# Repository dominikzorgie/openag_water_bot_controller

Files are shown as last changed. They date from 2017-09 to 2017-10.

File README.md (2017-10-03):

# OpenAg Waterbot Controller
Printed Circuit Board (PCB) that enables computer control for nutrient dosing in the Food Server (FS)

## Contents
- [Specification](documentation/spec.md) - High level description of the system.
- Bill of Materials
  - [PCB BOM](documentation/pcb_bom.csv) - all components required to assemble the PCB only. Includes microcontrollers, diodes, relays, resistors, etc.
  - [Enclosure BOM](documentation/enclosure_bom.csv) - All components required to assemble the encolsure around the PCB. Includes encapsulation shell, connectors, wire, potting, etc.
  - [Wiring Harness BOM](documentation/wiring_harness_bom.csv) - All components required to assemble the wiring harnesses for connecting the waterbot controller to the solenoids and brain box. Includes connectors, wires, heat shrink, etc.
  - [Tool BOM](documentation/tool_bom.csv) - All tools required to fabricate the enclosure and wire harnesses. Includes potting dispenser gun, powerpole crimper, etc.

## System Block Diagram
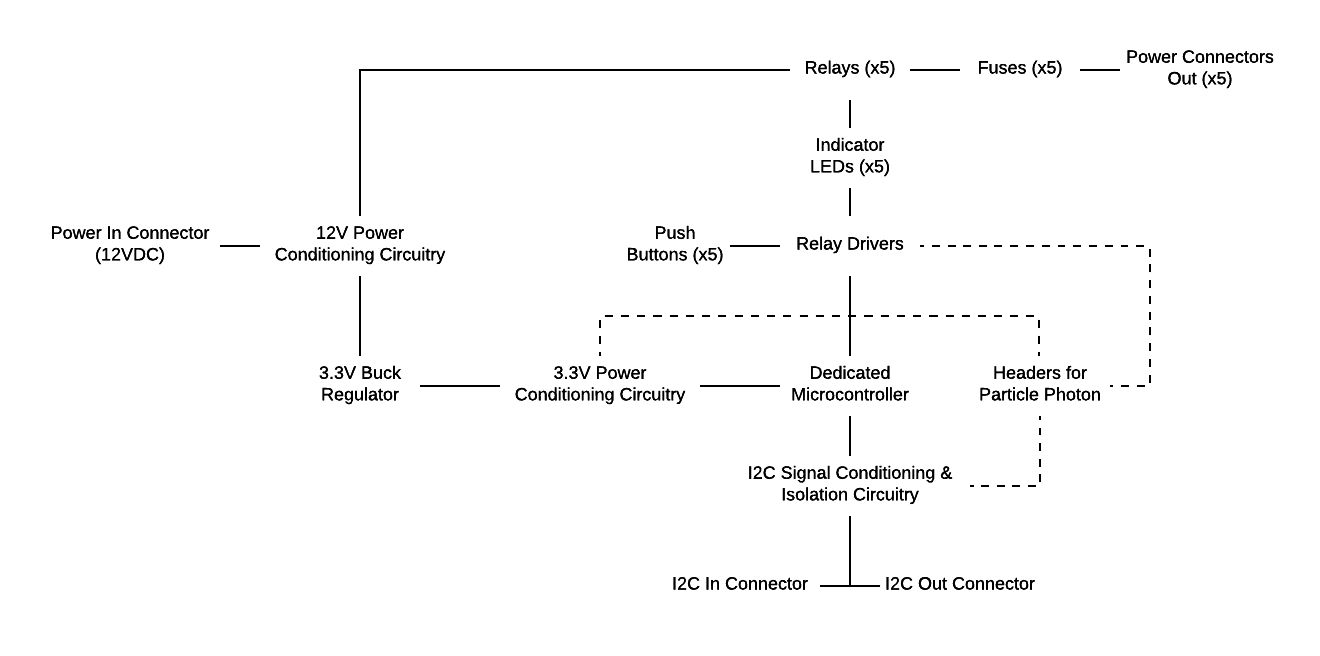
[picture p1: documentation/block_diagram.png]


## Connection Diagram
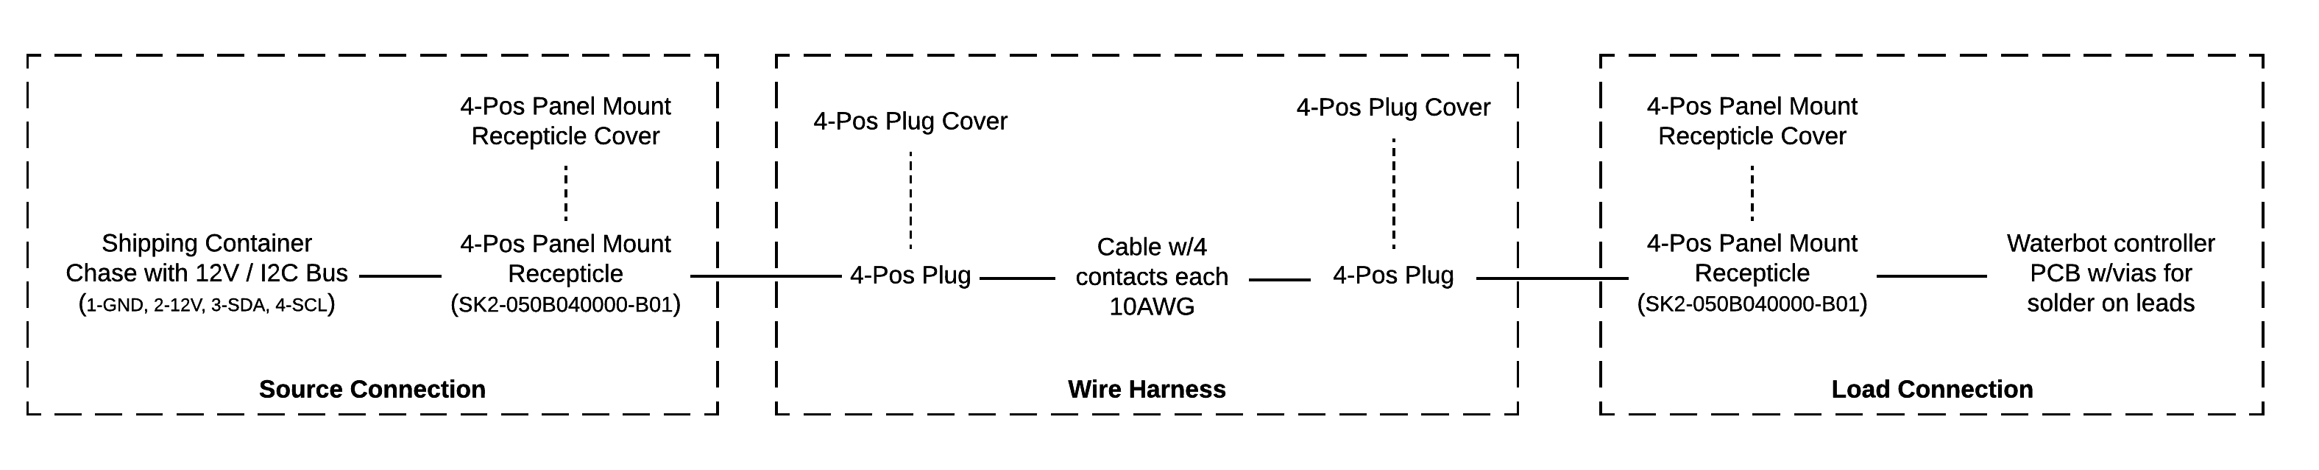
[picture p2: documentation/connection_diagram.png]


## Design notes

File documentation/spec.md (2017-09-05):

# OpenAg Water Bot Controller Specification

## Objective
The Open Agriculture Initiative at MIT's Media Lab is developing a Food Server, a shipping container sized unit outfitted with sensors and actuators for creating an automated control environment for hydroponic plant growth research.

A major component to the Food Server design is the Water Bot, a device for precisely controlling nutrient delivery to the plants. The Water Bot has five solenoid valves that must be controlled from a computer. The Water Bot Controller PCB will provide such control.

## Features
- Device will communicate via I2C with the Brain Box, the master control device built around the Beaglebone Black.
- Device will be powered from the 12VDC power lines running throughout the Food Server. 
- Device will be able to control the power to x5 12V-2A solenoids
- Device will have the option for manual control via pushbuttons that turn on/off the solenoids.
- Device will have a dedicated, low-cost onboard microcontroller that can be programmed to communicate via I2C and send high/low signals to the relay drivers to turn on/off the solenoids. 
- Device will have optional headers and zero-ohm resistor pads for connecting a Particle Photon in order to make the PCB a standalone IoT device. 
- Best practices will be followed to minimize electromagnetic interference throughout the device. 
- As the device will operate inside an environment that is subjected to high humidities and water splashing, all signal and power connectors will have an IP67 rating and the assembled PCB (PCBA) will be conformally coated.
- Device will integrate with mechanical mount on the side of each grow rack. The PCB will be no larger than 8"x8"

## Block Diagram
Block Diagram

## Supporting Documents
- Brain PCB V1 schematic & board files 
- Brain PCB V1 datasheets
- Example PSoC 4000 schematic & board files

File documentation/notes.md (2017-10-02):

on psoc4000 micro, for power config, using unregulated external supply
see fig 9 in datasheet
why are we using 1uF instead of 0.1uF?

what logic level i2c should we use?
psoc4000 provides a separate voltage domain for P3.0, P3.1, P3.2 via VDDIO
P3.0 and P3.1 are also SDAT and SCLK respectively
enables communicating w/system running at different voltage (VDDIO < VDD)
e.g. VDD can be 3.3V and VDDIO can be 1.8V
---never mind, the 16 pin SOIC does not have a VDDIO pin

what is the current draw on micro?..trying to spec voltage regulator
input voltage is 12V, output voltage is 3.3V
I_dd_11 max 4.5mA (when in active mode executing from flash w/cpu at 16mhz...see table 4)
Idiode max 100uA (table 6)
Itot_gpio max 85 mA (table 6)
spec regulator for >100mA

current draw on relay coil?
- @12VDC, 33.3mA

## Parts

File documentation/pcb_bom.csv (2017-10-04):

Qty | Description | Unit Cost | Sum Cost | MFG | MFG P/N | Vendor | Vendor P/N | Link
MICROCONTROLLERS
1 | IC MCU 32BIT 8KB FLASH 16SOIC | 1.18 | 1.18 | Cypress Semiconductor Corp | CY8C4013SXI-411 | Digikey | CY8C4013SXI-411-ND | https://www.digikey.com/product-detail/en/cypress-semiconductor-corp/CY8C4013SXI-411/CY8C4013SXI-411-ND/4842997
REGULATORS
1 | IC REG LINEAR 5V 100MA SOT23-3 | 0.92 | 0.92 | Texas Instruments | LM3480IM3-5.0/NOPB | Digikey | LM3480IM3-5.0/NOPBCT-ND | https://www.digikey.com/product-detail/en/texas-instruments/LM3480IM3-5.0-NOPB/LM3480IM3-5.0-NOPBCT-ND/270751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
DIODES
? | DIODE GEN PURP 75V 200MA SOT23-3 | 0.2 | ? | Diodes Incorporated | MMBD4148-7-F | Digikey | MMBD4148-FDICT-ND | https://www.digikey.com/product-detail/en/diodes-incorporated/MMBD4148-7-F/MMBD4148-FDICT-ND/815711
1 | TVS DIODE 14VWM 23.2VC SMA | 0.42 | 0.42 | Littlefuse | SMAJ14A | Digikey | SMAJ14ALFCT-ND | https://www.digikey.com/product-detail/en/littelfuse-inc/SMAJ14A/SMAJ14ALFCT-ND/762486
? | LED BLUE CLEAR 0603 SMD | 0.49 | ? | Kingbright | APT1608QBC/D | Digikey | 754-1434-1-ND | https://www.digikey.com/product-detail/en/kingbright/APT1608QBC-D/754-1434-1-ND/2163792
CAPACITORS
1 | CAP CER 0.1UF 50V X7R 1206 | 0.69 | 0.69 | Johansen Dielectrics | 500X18W104MV4E | Digikey | 709-1013-1-ND | https://www.digikey.com/product-detail/en/johanson-dielectrics-inc/500X18W104MV4E/709-1013-1-ND/1556418
RELAYS
? | RELAY GEN PURPOSE SPDT 10A 12V | 1.33 | ? | Omron Electronics | G5LE-14 DC12 | Digikey | Z1012-ND | https://www.digikey.com/product-detail/en/omron-electronics-inc-emc-div/G5LE-14-DC12/Z1012-ND/280369
SWITCHES
? | SWITCH TACTILE SPST-NO 0.05A 24V | 0.37 | ? | Omron Electronics | B3F-1020 | Digikey | SW402-ND | https://www.digikey.com/products/en?keywords=B3F-1020
ISOLATORS
1 | DGTL ISO 2.5KV 2CH I2C 8SOIC | 4.91 | 4.91 | Texas Instruments | ISO1540DR | Digikey | 296-34871-1-ND | https://www.digikey.com/product-detail/en/texas-instruments/ISO1540DR/296-34871-1-ND/3587214

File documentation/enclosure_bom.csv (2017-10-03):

Qty | Description | Unit Cost | Sum Cost | MFG | MFG P/N | Vendor | Vendor P/N | Link
 | 4-POS CONNECTOR SHELL
1 | 4 POSITION SPEC PAK PANEL MOUNT RECEPTACLE SHELL KIT | 6.96 | 6.96 | Anderson Power Products | SK2-050B04 | Anderson Power Products | SK2-050B04 | http://store.andersonpower.com/Search.aspx
1 | 4 POSITION SPEC PAK RECEPTACLE COVER KIT | 3.98 | 3.98 | Anderson Power Products | SK9-050 | Anderson Power Products | SK9-050 | http://store.andersonpower.com/Search.aspx
 | 6-POS CONNECTOR SHELL
1 | 6 POSITION SPEC PAK PANEL MOUNT RECEPTACLE SHELL KIT | 9.91 | 9.91 | Anderson Power Products | SK2-053B06 | Anderson Power Products | SK2-053B06 | http://store.andersonpower.com/Search.aspx
1 | 6 POSITION SPEC PAK RECEPTACLE COVER KIT | 5.04 | 5.04 | Anderson Power Products | SK9-053 | Anderson Power Products | SK9-053 | http://store.andersonpower.com/Search.aspx
 | CONNECTOR HOUSINGS
6 | POWERPOLE15/45 RED HOUSING | 0.34 | 2.04 | Anderson Power Products | 1327-BK | Anderson Power Products | 1327-BK | http://store.andersonpower.com/Search.aspx
2 | POWERPOLE15/45 BLACK HOUSING | 0.34 | 0.68 | Anderson Power Products | 1327G6-BK | Anderson Power Products | 1327G6-BK | http://store.andersonpower.com/Search.aspx
1 | POWERPOLE15/45 WHITE HOUSING | 0.34 | 0.34 | Anderson Power Products | 1327G7-BK | Anderson Power Products | 1327G7-BK | http://store.andersonpower.com/Search.aspx
1 | POWERPOLE15/45 YELLOW HOUSING | 0.34 | 0.34 | Anderson Power Products | 1327G16-BK | Anderson Power Products | 1327G16-BK | http://store.andersonpower.com/Search.aspx
 | CONNECTOR CONTACTS
10 | 20-16 AWG SILVER LOW DETENT CONTACT FOR POWERPOLE 15/45 | 0.20 | 2.00 | Anderson Power Products | 1332-BK | Anderson Power Products | 1332-BK | http://store.andersonpower.com/Search.aspx
 | POTTING
? | Dow Corning SE 4445 CV Thermally Conductive Gel Gray 210 mL Cartridge | 115.73 | ? | Dow Corning | 4025973 | Ellsworth Adhesives | SE 4445 CV KIT 210ML | https://www.ellsworth.com/products/by-market/consumer-products/thermally-conductive-materials/encapsulants/dow-corning-se-4445-cv-thermally-conductive-gel-gra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
 | ENCAPSULATION SHELL
 | Look on Maryland Plastic Products or Mouser 'Potting Box'

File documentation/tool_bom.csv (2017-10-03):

Qty | Description | Unit Cost | Sum Cost | MFG | MFG P/N | Vendor | Vendor P/N | Link
1 | Sulzer Mixpac EADM200-01 System 200 Manual Gun 200 mL 1 to 1 or 2 to 1 | 228.80 | 228.80 | ? | ? | Ellsworth Adhesives | EADM200-01 | https://www.ellsworth.com/products/dispensing-equipment-supplies/dispensing-systems-fluid/hand-held-2-part-applicators/sulzer-mixpac-eadm200-01-system-200-man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
1 | TAH EA250-24 Series 160 Plastic Spiral Bell Mixer 0.250 x 24 Element | 65.50 | 65.50 | ? | ? | Ellsworth Adhesives | EA250-24 | https://www.ellsworth.com/products/dispensing-equipment-supplies/tips-needles-nozzles-static-mixers/static-mixing-nozzles/tah-ea250-24-series-160-plastic-spir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
 | Powerpole crimping tool

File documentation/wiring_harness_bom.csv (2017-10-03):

Qty | Description | Unit Cost | Sum Cost | MFG | MFG P/N | Vendor | Vendor P/N | Link
 | 4-POS CONNECTOR SHELL
2 | 4 POSITION SPEC PAK PLUG SHELL KIT | 6.01 | 12.02 | Anderson Power Products | SK6-050B04 | Anderson Power Products | SK6-050B04 | http://store.andersonpower.com/Search.aspx
2 | 4 POSITION/SOLAR SPEC PAK STRAIGHT SHORT THREAD CABLE GLAND (PS01) | 2.27 | 4.54 | Anderson Power Products | PS1P16-10X | Anderson Power Products | PS1P16-10X | http://store.andersonpower.com/Search.aspx
2 | 4 POSITION SPEC PAK PLUG COVER KIT | 4.29 | 8.58 | Anderson Power Products | SK9P-050 | Anderson Power Products | SK9P-050 | http://store.andersonpower.com/Search.aspx
 | 6-POS CONNECTOR SHELL
1 | 6 POSITION SPEC PAK PLUG SHELL KIT | 9.34 | 9.34 | Anderson Power Products | SK6-053B06 | Anderson Power Products | SK6-053B06 | http://store.andersonpower.com/Search.aspx
1 | 6 POSITION SPEC PAK STRAIGHT SHORT THREAD CABLE GLAND (PS01) | 2.57 | 2.57 | Anderson Power Products | PS1P21-16X | Anderson Power Products | PS1P21-16X | http://store.andersonpower.com/Search.aspx
 | CONNECTOR HOUSINGS
6 | POWERPOLE15/45 RED HOUSING | 0.34 | 2.04 | Anderson Power Products | 1327-BK | Anderson Power Products | 1327-BK | http://store.andersonpower.com/Search.aspx
2 | POWERPOLE15/45 BLACK HOUSING | 0.34 | 0.68 | Anderson Power Products | 1327G6-BK | Anderson Power Products | 1327G6-BK | http://store.andersonpower.com/Search.aspx
1 | POWERPOLE15/45 WHITE HOUSING | 0.34 | 0.34 | Anderson Power Products | 1327G7-BK | Anderson Power Products | 1327G7-BK | http://store.andersonpower.com/Search.aspx
1 | POWERPOLE15/45 YELLOW HOUSING | 0.34 | 0.34 | Anderson Power Products | 1327G16-BK | Anderson Power Products | 1327G16-BK | http://store.andersonpower.com/Search.aspx
 | CONNECTOR CONTACTS
10 | 20-16 AWG SILVER LOW DETENT CONTACT FOR POWERPOLE 15/45 | 0.20 | 2.00 | Anderson Power Products | 1332-BK | Anderson Power Products | 1332-BK | http://store.andersonpower.com/Search.aspx
 | WIRE
 | Extend solenoid wires?
 | Cable with 4 conductors?
 | HEAT SHRINK

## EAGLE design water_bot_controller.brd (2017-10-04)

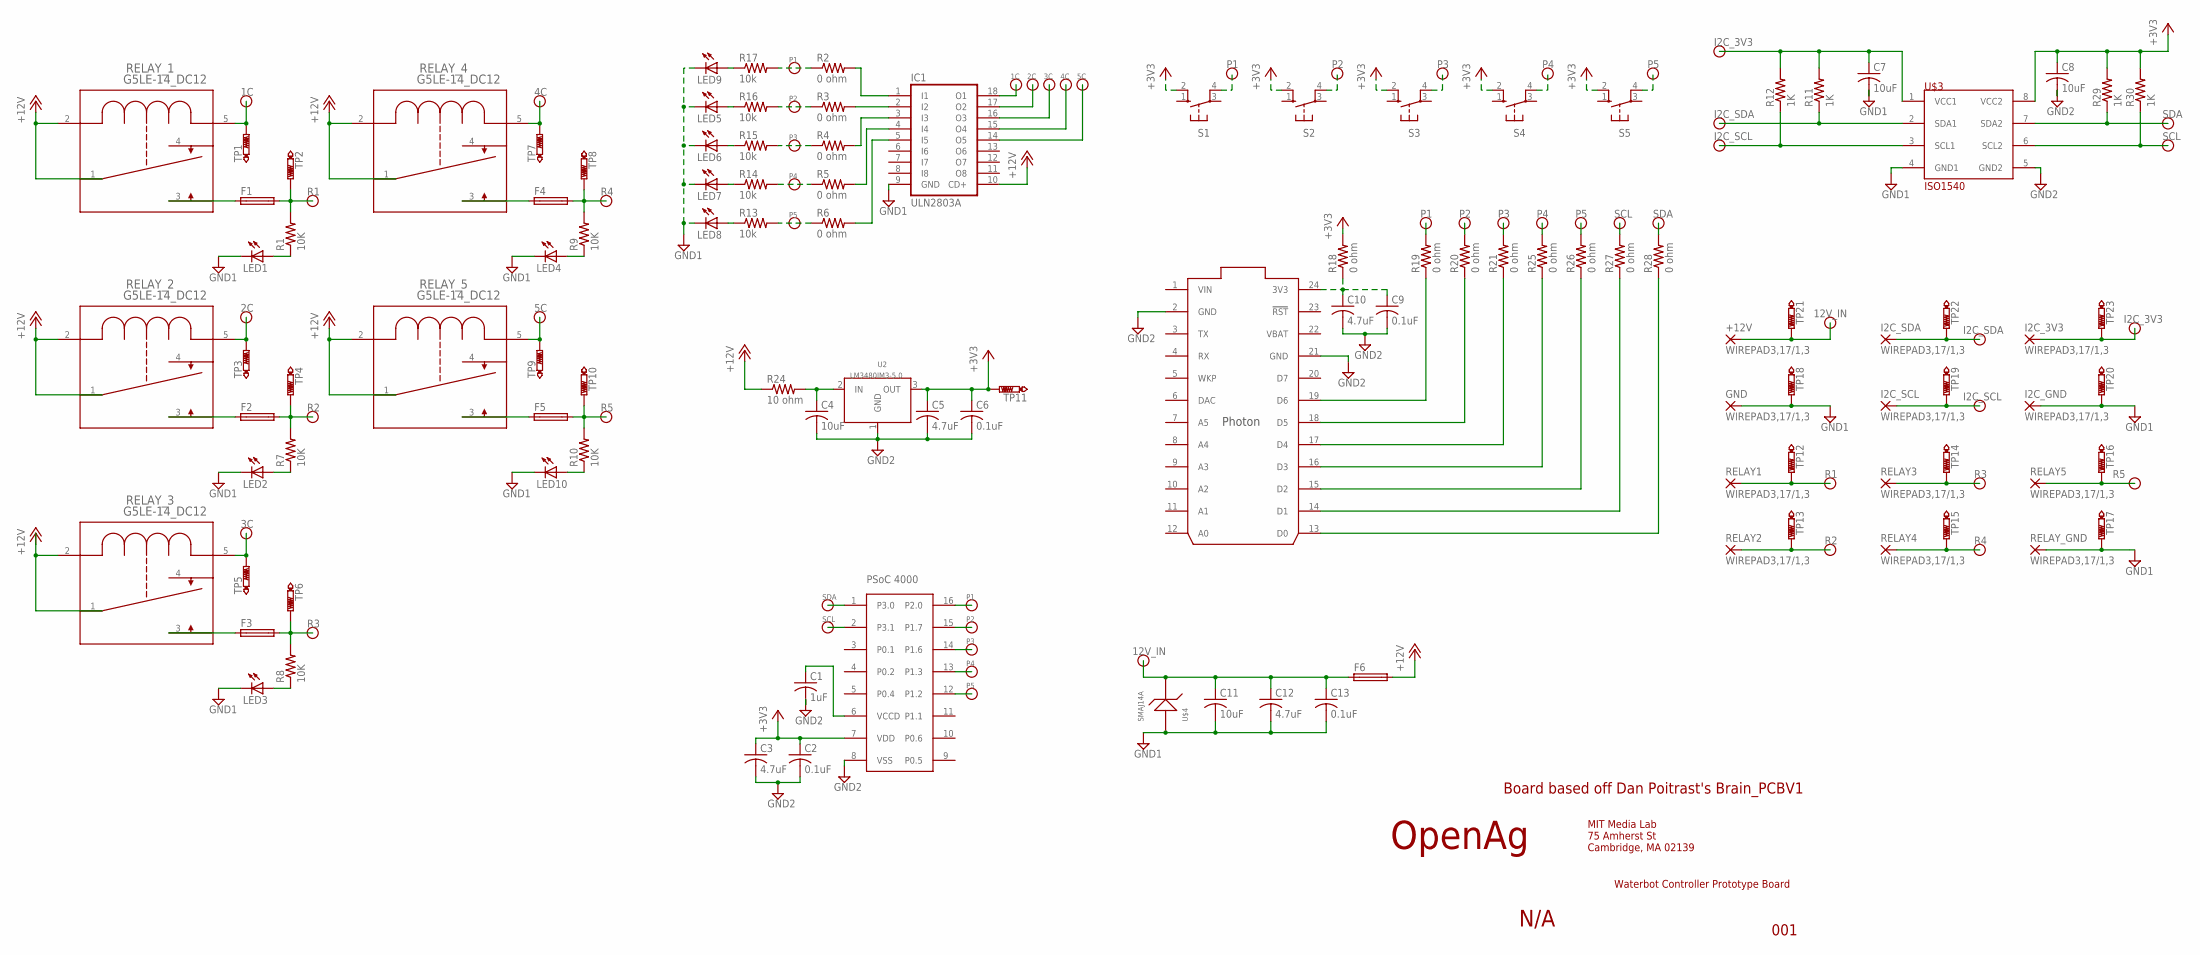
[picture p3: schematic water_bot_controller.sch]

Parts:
+12V: WIREPAD3,17/1,3; 3,17/1,3
C1: 1uF; C0603
C2, C6, C9, C13: 0.1uF; C0603
C3, C5, C10, C12: 4.7uF; C1206
C4, C7, C8, C11: 10uF; C1206
F1, F2, F3, F4, F5, F6: GSH15
GND: WIREPAD3,17/1,3; 3,17/1,3
I2C_3V3, I2C_GND, I2C_SCL, I2C_SDA: WIREPAD3,17/1,3; 3,17/1,3
IC1: ULN2803A; DIL18
LED1, LED2, LED3, LED4, LED5, LED6, LED7, LED8, LED10: LEDCHIP-LED0603; CHIP-LED0603
LED9: LED; SMARTLED-TTW
R1, R7, R8, R9, R10: 10K; R0603
R2, R3, R4, R5, R6, R18, R19, R20, R21, R25, R26, R27, R28: 0 ohm; R0603
R11, R12, R29, R30: 1K; R0603
R13, R14, R15, R16, R17: 10k; R0603
R24: 10 ohm; R0603
RELAY1, RELAY2, RELAY3, RELAY4, RELAY5: WIREPAD3,17/1,3; 3,17/1,3
RELAY_1, RELAY_2, RELAY_3, RELAY_4, RELAY_5: G5LE-14_DC12; RELAY_G5LE-1
RELAY_GND: WIREPAD3,17/1,3; 3,17/1,3
S1, S2, S3, S4, S5: 10-XX; B3F-10XX
TP1, TP2, TP3, TP4, TP5, TP6, TP7, TP8, TP9, TP10, TP11, TP12, TP13, TP14, TP15, TP16, TP17, TP18, TP19, TP20, TP21, TP22, TP23: PTR1B2,54; B2,54
U2: LM3480IM3-5.0; SOT-23
U$1: PSOC_4000; SOIC16
U$2: PHOTON_WITH_HEADERS; PHOTON
U$3: ISO1540; SOIC8
U$4: SMAJ14A; DO-214AC

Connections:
1C: IC1.18 (O1), RELAY_1.5, TP1.TP
2C: IC1.17 (O2), RELAY_2.5, TP3.TP
3C: IC1.16 (O3), RELAY_3.5, TP5.TP
4C: IC1.15 (O4), RELAY_4.5, TP7.TP
5C: IC1.14 (O5), RELAY_5.5, TP9.TP
12V_IN: +12V.1, C11.1, C12.1, C13.1, F6.1, TP21.TP, U$4.C
+3V3: C2.1, C3.1, C5.1, C6.1, C8.1, R18.2, R29.2, R30.2, S1.2 (S1), S2.2 (S1), S3.2 (S1), S4.2 (S1), S5.2 (S1), TP11.TP, U2.3 (OUT), U$1.7 (VDD), U$3.8 (VCC2)
+12V: F6.2, IC1.10 (CD+), R24.1, RELAY_1.1 (2), RELAY_1.2 (1), RELAY_2.1 (2), RELAY_2.2 (1), RELAY_3.1 (2), RELAY_3.2 (1), RELAY_4.1 (2), RELAY_4.2 (1), RELAY_5.1 (2), RELAY_5.2 (1)
GND1: C7.2, C11.2, C12.2, C13.2, GND.1, I2C_GND.1, IC1.9 (GND), LED1.C, LED2.C, LED3.C, LED4.C, LED5.C, LED6.C, LED7.C, LED8.C, LED9.C@1 (C), LED10.C, RELAY_GND.1, TP17.TP, TP18.TP, TP20.TP, U$3.4 (GND1), U$4.A
GND2: C1.2, C2.2, C3.2, C4.2, C5.2, C6.2, C8.2, C9.2, C10.2, U2.1 (GND), U$1.8 (VSS), U$2.2 (GND), U$2.21 (GND), U$3.5 (GND2)
I2C_3V3: C7.1, I2C_3V3.1, R11.2, R12.2, TP23.TP, U$3.1 (VCC1)
I2C_SCL: I2C_SCL.1, R12.1, TP19.TP, U$3.3 (SCL1)
I2C_SDA: I2C_SDA.1, R11.1, TP22.TP, U$3.2 (SDA1)
unnamed: LED1.A, R1.1
unnamed: F1.1, RELAY_1.3
unnamed: F2.1, RELAY_2.3
unnamed: LED2.A, R7.1
unnamed: IC1.1 (I1), R2.2
unnamed: IC1.3 (I3), R4.2
unnamed: IC1.5 (I5), R6.2
unnamed: IC1.4 (I4), R5.2
unnamed: F3.1, RELAY_3.3
unnamed: LED3.A, R8.1
unnamed: F4.1, RELAY_4.3
unnamed: LED9.A@1 (A), R17.1
unnamed: LED5.A, R16.1
unnamed: LED6.A, R15.1
unnamed: LED7.A, R14.1
unnamed: LED8.A, R13.1
unnamed: LED4.A, R9.1
unnamed: F5.1, RELAY_5.3
unnamed: LED10.A, R10.1
unnamed: R26.1, U$2.15 (D2)
unnamed: R27.1, U$2.14 (D1)
unnamed: C9.1, C10.1, R18.1, U$2.24 (3V3)
unnamed: R19.1, U$2.19 (D6)
unnamed: R20.1, U$2.18 (D5)
unnamed: R21.1, U$2.17 (D4)
unnamed: R25.1, U$2.16 (D3)
unnamed: R28.1, U$2.13 (D0)
unnamed: C1.1, U$1.6 (VCCD)
unnamed: C4.1, R24.2, U2.2 (IN)
P1: R2.1, R17.2, R19.2, S1.4 (P1), U$1.16 (P2.0)
P2: R3.1, R16.2, R20.2, S2.4 (P1), U$1.15 (P1.7)
P3: R4.1, R15.2, R21.2, S3.4 (P1), U$1.14 (P1.6)
P4: R5.1, R14.2, R25.2, S4.4 (P1), U$1.13 (P1.3)
P5: R6.1, R13.2, R26.2, S5.4 (P1), U$1.12 (P1.2)
R1: F1.2, R1.2, RELAY1.1, TP2.TP, TP12.TP
R2: F2.2, R7.2, RELAY2.1, TP4.TP, TP13.TP
R3: F3.2, R8.2, RELAY3.1, TP6.TP, TP14.TP
R4: F4.2, R9.2, RELAY4.1, TP8.TP, TP15.TP
R5: F5.2, R10.2, RELAY5.1, TP10.TP, TP16.TP
SCL: R27.2, R30.1, U$1.2 (P3.1), U$3.6 (SCL2)
SDA: R28.2, R29.1, U$1.1 (P3.0), U$3.7 (SDA2)
VBAT: U$2.22 (VBAT)
VIN: U$2.1 (VIN)

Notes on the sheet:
Waterbot Controller Prototype Board
OpenAg
MIT Media Lab 75 Amherst St Cambridge, MA 02139
N/A
001
Board based off Dan Poitrast's Brain_PCBV1
LM3480IM3-5.0

Board: 2 copper layers, 108 parts (0 on the bottom side), 54 nets, no tracks yet.

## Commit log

2017-09-05 added relay circuitry
    [water_bot_controller.brd, water_bot_controller.sch]
2017-09-19 added microcontroller module, cleaned up relay driver module
    [bom.csv, water_bot_controller.brd, water_bot_controller.sch]
2017-10-02 cleaned up relay module
    [bom.csv, water_bot_controller.brd, water_bot_controller.sch]
2017-10-02 added connection diagram option
    [bom.csv]
2017-10-02 restructured files
    [bom.csv]
2017-10-03 spec'd pwr/sig conns, added pushbuttons to schematic
    [enclosure_bom.csv, pcb_bom.csv, tool_bom.csv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]
2017-10-03 added optional particle photon headers
    [water_bot_controller.brd, water_bot_controller.sch]
2017-10-04 added i2c isolation circuitry, replaced leds, and added test points
    [pcb_bom.csv, water_bot_controller.brd, water_bot_controller.sch]
2017-10-04 added 12v power conditioning
    [pcb_bom.csv, water_bot_controller.brd, water_bot_controller.sch]
